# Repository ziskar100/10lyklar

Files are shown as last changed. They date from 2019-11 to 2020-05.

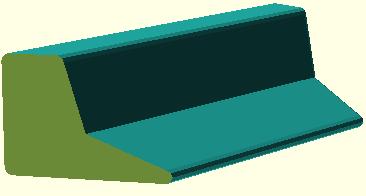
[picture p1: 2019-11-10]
initial_ideas/first_3d_printed_materials/garbage_collector/ArmLeft.jpg

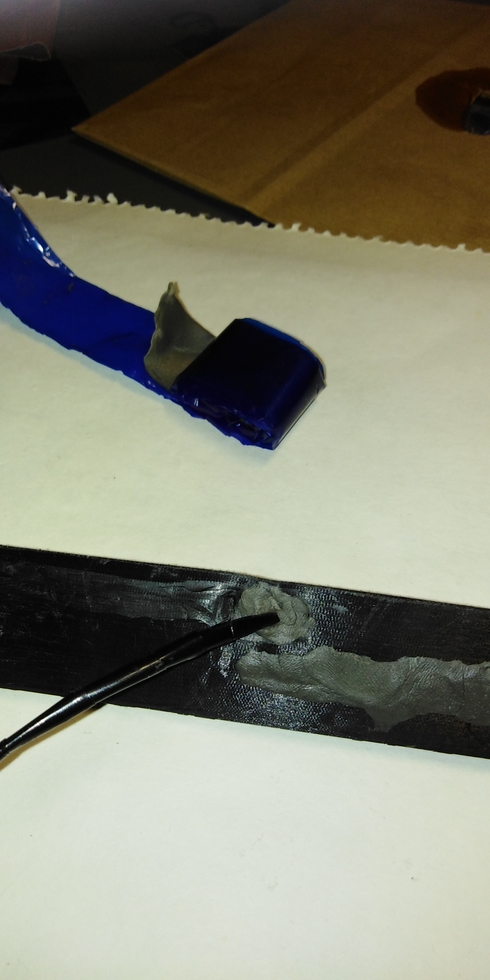
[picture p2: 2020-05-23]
3dprinting/construction_details/dcmotor_cables_at_the exit_of_hull.jpg

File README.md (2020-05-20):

# To Oceanis
Αποθετήριο του 10ου Γενικού Λυκείου Λάρισας για στην συμμετοχή στον Διαγωνισμό Ρομποτικής Ανοιχτών Τεχνολογιών

### Τίτλος έργου
Το SOS των ωκεανών· Η αποστολή του OCEANIS

### Αναλυτική περιγραφή ιδέας:

Η πρότασή μας σχετίζεται άμεσα με το ζήτημα της κλιματικής αλλαγής και ειδικότερα με την Προστασία του περιβάλλοντος. Σήμερα στους ωκεανούς, στα ποτάμια και στις λίμνες συσσωρεύονται  αμέτρητοι τόνοι σκουπιδιών από τις καθημερινές δραστηριότητες του ανθρώπου-καταναλωτή με δραματικά αποτελέσματα για την βιοποικιλότητα των υδάτινων περιβαλλόντων και στην τελική για την ίδια την επιβίωση του ανθρώπινου γένους μακροπρόθεσμα.

Επομένως, καθίσταται επιτακτική η ανάγκη εξεύρεσης λύσης καθαρισμού σημαντικού τουλάχιστον μέρους, των σκουπιδιών για την ανακούφιση των τεράστιων αυτών υδατικών λεκανών.

Για το σκοπό αυτό προτείνουμε ένα πρωτότυπο αυτοκινούμενο θαλάσσιο σκάφος που το ονομάσαμε Oceanis. Αυτό, στην τελική του εκδοχή θα κινείται μέσω ηλιακής ενέργειας αυτόνομα, ενώ στην παρούσα υλοποίηση θα χρησιμοποιηθεί η ανοιχτού τύπου τεχνολογία Arduino. Το σκάφος θα σχεδιασθεί από την αρχή μέσω ανοιχτού λογισμικού CAD (OpenSCAD) και θα εκτυπωθεί εξολοκλήρου στον διαθέσιμο 3D εκτυπωτή ULTIMAKER 3 του σχολείου (δείτε τις ήδη έτοιμες εικόνες του Oceanis στα αρχεία εικόνων του github).

Το Oceanis θα κινείται στο νερό με τη βοήθεια δύο (2) κινητήρων (δείτε τον κατάλογο υλικών) με δυνατότητα ελέγχου τους μέσω εφαρμογής με κινητό. Για την εφαρμογή θα χρησιμοποιηθεί το ανοιχτό λογισμικό AppInventor και η επικοινωνία θα γίνεται με bluetooth (δείτε τον κατάλογο υλικών). Το Oceanis θα συλλέγει τα σκουπίδια μέσω μιας ταινίας - ενός ιμάντα - μεταφοράς που θα κινείται με ειδικό κινητήρα (δείτε τον κατάλογο υλικών) ελεγχόμενο απευθείας από το Arduino.

Παράλληλα το Oceanis θα συλλέγει με δύο (2) ειδικούς αισθητήρες (δείτε τον κατάλογο υλικών) επιστημονικά δεδομένα του υδάτινου περιβάλλοντος (θερμοκρασία και καθαρότητα νερού) και θα τα στέλνει με τη βοήθεια ειδικού αισθητήρα (δείτε τον κατάλογο υλικών) και του Arduino στο cloud σε μια πλατφόρμα IoT που με τη σειρά της θα μας τα διαθέτει μέσω Internet στις συσκευές μας (Η/Υ, tablet, κινητό), ώστε να παρακολουθούμε αυτά τα δεδομένα μέσω γραφικών παραστάσεων.

### Λίστα προτεινόμενου εξοπλισμού:
Ως υλικά hardware θα χρησιμοποιηθούν:

1. Για τον σχεδιασμό και κατασκευή του project Oceanis:
-1x Arduino UNO     [~7€]

-1x Breadboard

-xJumper wires and Resistors

-1x 9 volt battery rechargeable    [~8€]

-1x 9 volt battery connector     [~0.5€]

-1x Bluetooth module HC-06      [~7€]

-1x L293D IC     [~1€]

-2x DC motors     [~6€]

-1x Stepper motor     [~3€]

-1x DS18B20 Waterproof Temperature Sensor    [~3.5€]

-1x Analog Turbidity Sensor for Arduino     [~13€]

-1x ESP8266 wifi module     [~5€]

-1x Fillament for 3d printer     [~17€]

-Μεταφορικά      [~4€]

2. Για τον προγραμματισμό  θα χρησιμοποιηθούν:

-Περιβάλλον προγραμματισμού Arduino IDE (ελεύθερο λογισμικό)

-Περιβάλλον προγραμματισμού AppInventor (ελεύθερο λογισμικό)

-Ρυθμίσεις πλατφόρμας IoT (ελεύθερης πρόσβασης)

### Ενδεικτικό κόστος:
95 Ευρώ

Σε κάθε φάκελο υπάρχει ένα αντίστοιχο Readme όπου εξηγούνται τα περιεχόμενα το φακέλου αυτού.

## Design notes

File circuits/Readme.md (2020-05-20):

## Τι περιέχει ο φάκελος
Στον φάκελο αυτό μπορείτε να πάρετε μια συνολική εικόνα όλου του ηλεκτρονικού σχεδιασμού του έργου. Επίσης υπάρχουν 4 υποφάκελοι που ανά δύο μας δείχνουν λεπτομερειακά τα δύο υποσυστήματα, των κινητήρων και των αισθητήρων νερού, δηλ. μπορείτε να δείτε τις συνδεσμολογίες τους και πως είναι στην πραγματικότητα, αλλά και πως είναι ιδεατά σχηματικά για πλήρη κατανόηση των πραγμάτων.

Ωστόσο, αξίζει τον κόπο να αναφερθούμε εδώ ιδιαίτερα στους δύο αισθητήρες παρακολούθησης του νερού που επιλέχθηκαν για το σκοπό αυτό.
### Αισθητήρας θολότητας ή θολούρας ή θολερότητας (Turbidity Sensor V1.0)
Ο αισθητήρας αυτός προσδιορίζει όσον αφορά την ποιότητα του νερού σε τι επίπεδο βρίσκεται από πλευράς θολότητας. Μπορεί και ανιχνεύει διάφορα αιωρούμενα στερεά σωματίδια (TSS) στο νερό. Αυτό το πετυχαίνει μετρώντας τη διαπερατότητα του φωτός και το ρυθμό σκέδασης που αλλάζει με την ποσότητα των ολικών αιωρούμενων σωματιδίων στο νερό. Όταν αυξάνεται η τιμή του TTS, τότε αυξάνεται το επίπεδο θολότητας του νερού και γενικότερα ενός υγρού.
 
Ο συγκεκριμένος αισθητήρας διαθέτει λειτουργίες εξόδου αναλογικού (Analog) και ψηφιακού (Digital) σήματος. Μπορούμε να επιλέξουμε όποια λειτουργία θέλουμε, καθώς επίσης και να ρυθμίσουμε το κατώφλι (threshold) μέσω ποτενσιόμετρου όταν βρισκόμαστε σε λειτουργία ψηφιακού σήματος.
 
Οι αισθητήρες θολότητας μπορούν να χρησιμοποιηθούν για τη μέτρηση της ποιότητας των υδάτων σε ποτάμια και ρέματα, μετρήσεις λυμάτων και αποβλήτων, έρευνα μεταφοράς ιζημάτων και εργαστηριακές μετρήσεις.

Πηγή: https://wiki.dfrobot.com/Turbidity_sensor_SKU__SEN0189
 
### Αισθητήρας θερμοκρασίας με αδιάβροχο καλώδιο προέκτασης (Waterproof DS18b20 temperature probe temperature sensor 18B20 for Arduino)
 
Κάθε αισθητήρας θερμοκρασίας DS18B20 έχει έναν μοναδικό σειριακό κωδικό 64-bit. Αυτό μας επιτρέπει να συνδέουμε πολλούς αισθητήρες στο ίδιο καλώδιο δεδομένων. Έτσι, μπορούμε να παίρνουμε θερμοκρασία από πολλούς αισθητήρες χρησιμοποιώντας μόνο έναν ψηφιακό pin στο Arduino μας.

Πηγή: https://randomnerdtutorials.com/guide-for-ds18b20-temperature-sensor-with-arduino/

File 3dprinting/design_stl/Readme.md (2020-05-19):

## Τι περιέχει ο φάκελος
Εδώ θα μπορέσετε να κατεβάσετε όλα τα αρχεία πού δημιουργήθηκαν με το FreeCAD σε μορφή stl και κατόπιν να τα εισάγετε στο ειδικό πρόγραμμα Cura  για να δημιουργήσετε από τα αρχεία αυτά τα αντίστοιχα αρχεία τύπου gcode και τα οποία στη συνέχεια μπορείτε να εκτυπώσετε στο 3D Printer.

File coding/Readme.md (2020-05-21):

## Τι περιέχει ο φάκελος
Εδώ θα μπορέσετε να δείτε όλους τους κώδικες. Αναλυτικά θα δείτε τους εξής κώδικες:

### 1. Arduino_Bluetooth_DC_Motors.aia

Είναι ο κώδικας ελέγχου των κινητήρων σε μορφή επεξεργάσιμη μέσα από το περιβάλλον του AppInventor. Μπορείτε να τον κατεβάσετε και να τον εισάγετε ώστε να κάνετε τη δική σας επεξεργασία.

### 2. Arduino_Bluetooth_DC_Motors.apk

Είναι ο κώδικας ελέγχου των κινητήρων σε μορφή εκτελέσιμη. Μπορείτε να τον κατεβάσετε και να τον εγκαταστήσετε στην κινητή συσκευή σας και να την εκτελείτε όποτε θέλετε.

### 3. Motor_Stepper
Είναι ο κώδικας ελέγχου του βηματικού κινητήρα. Μπορείτε να τον χρησιμοποιήσετε για να δοκιμάσετε τη σωστή λειτουργία του. Απαιτείται η ενσωμάτωση της βιβλιοθήκης AFMotor.h

### 4. Motors_DCX2_Stepper_via_Bluetooth
Είναι ο κώδικας ελέγχου μέσω Bluetooth και των τριών κινητήρων. Απαιτείται οπωσδήποτε η ασπίδα ελέγχου των κινητήρων όπως φαίνεται και στις αντίστοιχες εικόνες. Η ασπίδα δίνει δύο ports, το port #1 (M1 & M2) όπου βάζουμε τον βηματικό κινητήρα με τη σειρά των 5 καλωδίων όπως φαίνεται και στην αντίστοιχη εικόνα και το port #2 (M3 & M4) όπου βάζουμε τα 4 καλώδια των DC κινητήρων όπως φαίνεται και στην αντίστοιχη εικόνα (η μεσαία θέση μένει κενή).

Στον κώδικα υπάρχουν αρκετά επεξηγηματικά σχόλια και θεωρείται σχετικά εύκολος στην κατανόηση. Εκείνο που αξίζει να δει κανείς είναι πως γίνεται η ζεύξη μεταξύ του κώδικα του Arduino με τα blocks του AppInventor. Γι αυτό και πρέπει να ανοιχτούν ταυτόχρονα οι δύο κώδικες. 

### 5. Motors_DCX2_via_Bluetooth

Είναι ο κώδικας ελέγχου μέσω Bluetooth των DC κινητήρων. Μπορείτε να τον χρησιμοποιήσετε για να δοκιμάσετε τη σωστή λειτουργία τους. Απαιτείται η ενσωμάτωση της βιβλιοθήκης AFMotor.h

### 7. WEMOS_D1_Wifi_Sensor

Είναι ο κώδικας αποστολής μέσω WiFi των δεδομένων των δύο αισθητήρων του νερού. Παρουσιάζει ιδιαίτερο εκπαιδευτικό ενδιαφέρον και είναι εμπλουτισμένος με αρκετές βιβλιοθήκες! Στο 1ο κομμάτι του ενσωματώνονται οι βιβλιοθήκες που φαίνονται στον κώδικα και επιλέγεται σαν συσκευή (προσοχή εδώ!) όχι το Arduino, αλλά το WEMOS D1 R1.

Στο 2ο κομμάτι εγκαθιδρύονται τα Wifi settings. Χρειάζεται να ξέρουμε για το δίκτυο Internet που συνδεόμαστε δύο πράγματα: To ssid και το password του δικτύου. Τα βάζουμε αντίστοιχα στη θέση των αστεριών.

Στο 3ο κομμάτι εγκαθιδρύονται τα ThingSpeak Settings . Πρέπει να ξέρει ο κώδικας 2 πληροφορίες από την πλατφόρμα ThingSpeak: Το channelID και το writeAPIKey. Εδώ αντικαθιστούμε με τα δικά μας αφού έχουμε ανοίξει λογαριασμό στην πλατφόρμα και φτιάξουμε ένα κανάλι με όσα πεδία επιθυμούμε. Κατόπιν ακολουθεί το setup και μετά το loop.

Στο loop, στο 1ο κομμάτι συλλέγουμε τις τιμές των αισθητήρων και κάνουμε τις κατάλληλες μετατροπές, ειδικά για τη θολότητα. Στο επόμενο κομμάτι δημιουργούμε ένα string που θα έχει όλες τις πληροφορίες ανά πεδίο και τις οποίες θα στείλουμε πάνω στην πλατφόρμα. Τέλος, στέλνουμε τα data στην πλατφόρμα και δημιουργούμε στο τέλος και μια χρονοκαθυστέρηση μεταξύ των αποστολών.

### 8. Water_DS18B20_Temperature_Sensor

Είναι ο κώδικας ελέγχου του αισθητήρα θερμοκρασίας. Μπορείτε να τον χρησιμοποιήσετε για να δοκιμάσετε τη σωστή λειτουργία του. Απαιτείται η ενσωμάτωση των βιβλιοθηκών OneWire.h και DallasTemperature.h

### 9. Water_Turbidity_Analog_Sensor

Είναι ο κώδικας ελέγχου του αισθητήρα θολότητας. Μπορείτε να τον χρησιμοποιήσετε για να δοκιμάσετε τη σωστή λειτουργία του.

### 10. prop-designer
Ο συγκεκριμένος κώδικας μας δίνει τη δυνατότητα να δημιουργούμε παραμετρικά ότι προπέλα επιθυμούμε, όσον αφορά είτε τον αριθμό των λεπίδων της, είτε το πάχος του άξονά της, είτε το μέγεθος του ομφαλού του άξονα κ.α.

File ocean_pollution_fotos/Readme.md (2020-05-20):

## Τι περιέχει ο φάκελος

Εδώ έχουμε μια συλλογή φωτογραφιών με την τεράστια ζημιά που υφίσταται το υδάτινο περιβάλλον και που προέκυψαν από την έρευνά μας.

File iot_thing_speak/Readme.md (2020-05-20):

## Τι περιέχει ο φάκελος
Εδώ θα μπορέσετε να δείτε δύο χαρακτηριστικές εικόνες από την πλατφόρμα ThingSpeak.

Η 1η δείχνει ένα στιγμιότυπο από τις 3 γραφικές παραστάσεις των μεγεθών που μετρούνται από τους αισθητήρες του νερού.

Η 2η  δείχνει μια από τις εξελιγμένες δυνατότητες που έχει η συγκεκριμένη πλατφόρμα.

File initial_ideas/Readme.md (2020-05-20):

## Τι περιέχει ο φάκελος
Εδώ θα μπορέσετε να δείτε:

1.  Μια εικόνα όλων παραγγελθέντων ειδών

2. Μια εικόνα όλων των εργαλείων που χρησιμοποιήθηκαν για την κατασκευή του έργου. Λείπει από την εικόνα το κολλητήρι.

3. Δύο υπο-φακέλους που αφορούν την αρχική φάση του έργου. Ο ένας περιέχει όλες τις αρχικές σκέψεις αποτυπωμένες στο χαρτί. Ο άλλος περιέχει αρχικές 3D εκτυπώσεις κομματιών του σκάφους, ώστε να πάρουμε μια αρχική ιδέα τι πρέπει να φτιάξουμε στη συνέχεια.

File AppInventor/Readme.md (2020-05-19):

## Τι περιέχει ο φάκελος
Εδώ θα μπορέσετε να δείτε δύο χαρακτηριστικές εικόνες από την εφαρμογή το AppInventor, η μία αφορά στο σχεδιασμό και η άλλη αφορά τα blocks (κώδικα).

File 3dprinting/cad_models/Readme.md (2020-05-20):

## Τι περιέχει ο φάκελος
Εδώ θα μπορέσετε να δείτε όλα τα επιμέρους σχέδια που εκπονήθηκαν με το ελεύθερο λογισμικό FreeCAD καθώς επίσης και με το OpenSCAD. Όσον αφορά το FreeCAD  μπορείτε να   πάρετε περισσότερες πληροφορίες από τον σύνδεσμο:
 
https://www.secnews.gr/202551/freecad-0-18-4-open-source-3d-dorean-cad-gia-olous/
 
Το FreeCAD είναι μια εφαρμογή CAD ανοικτού κώδικα που έχει σαν κύριο στόχο την μηχανολογική ανάπτυξη και το βιομηχανικό σχέδιο.
Σε αυτό βοηθάει ο αρθρωτός σχεδιασμός που επιτρέπει πάρα πολλές παραμετροποιήσεις για να χρησιμοποιηθεί και σε άλλες εφαρμογές. Υποστηρίζεται από μία πολύ δυναμική κοινότητα,  είναι γραμμένο σε Python και διατίθενται πάρα πολλά tutorials.

Όσον αφορά το Openscad όπως μας πληροφορεί και η ιστοσελίδα του ellak
 
https://openhardware.ellak.gr/2017/01/18/openscad-mia-efarmogi-eleftherou-logismikou-gia-3d-modeling/
 
είναι ένα λογισμικό για τη δημιουργία τρισδιάστατων CAD μοντέλων. Είναι ελεύθερο λογισμικό και διατίθεται σε διάφορες εκδόσεις για διαφορετικές πλατφόρμες λογισμικών, Linux/UNIX, Windows και Mac OS X και  εξαιρετικά χρήσιμο για όσους τυπώνουν 3D αντικείμενα και χρειάζονται ένα λογισμικό επεξεργασίας (για αρχεία του αποθετηρίου Thingiverse) και 3D modeling.

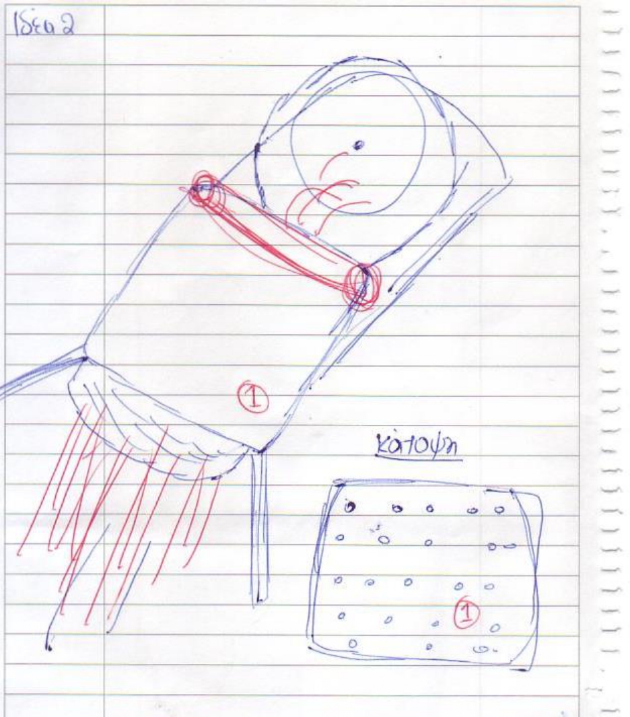
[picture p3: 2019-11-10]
initial_ideas/paper_sketch_plans/plan2.jpg

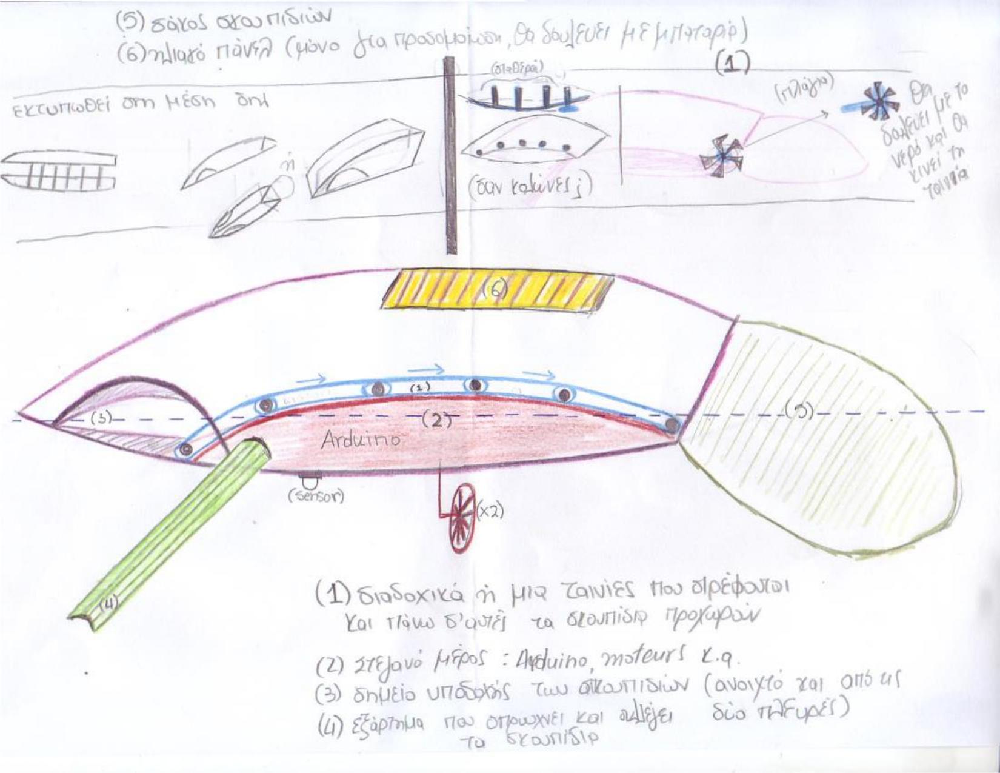
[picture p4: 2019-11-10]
initial_ideas/paper_sketch_plans/plan6.jpg

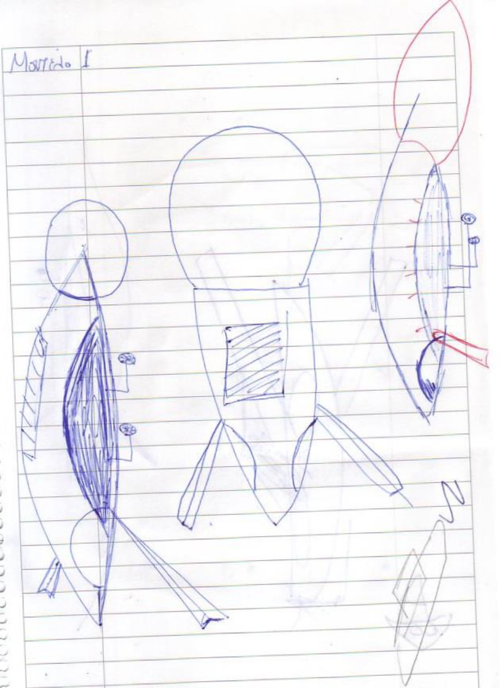
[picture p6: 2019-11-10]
initial_ideas/paper_sketch_plans/plan4.jpg

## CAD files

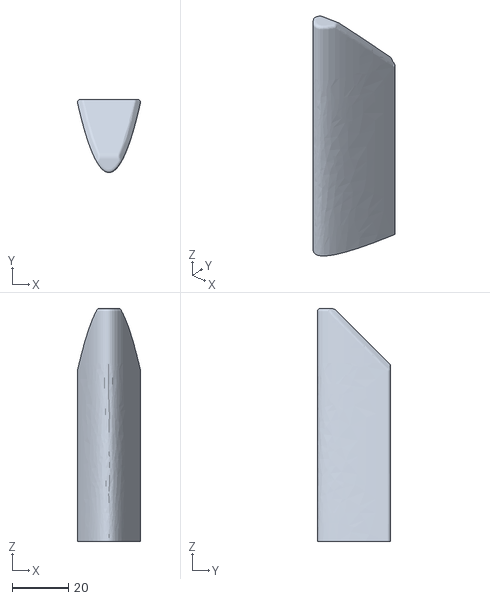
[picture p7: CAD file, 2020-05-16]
3dprinting/design_stl/Hull_Front.stl
22.5 x 26.0 x 83.0

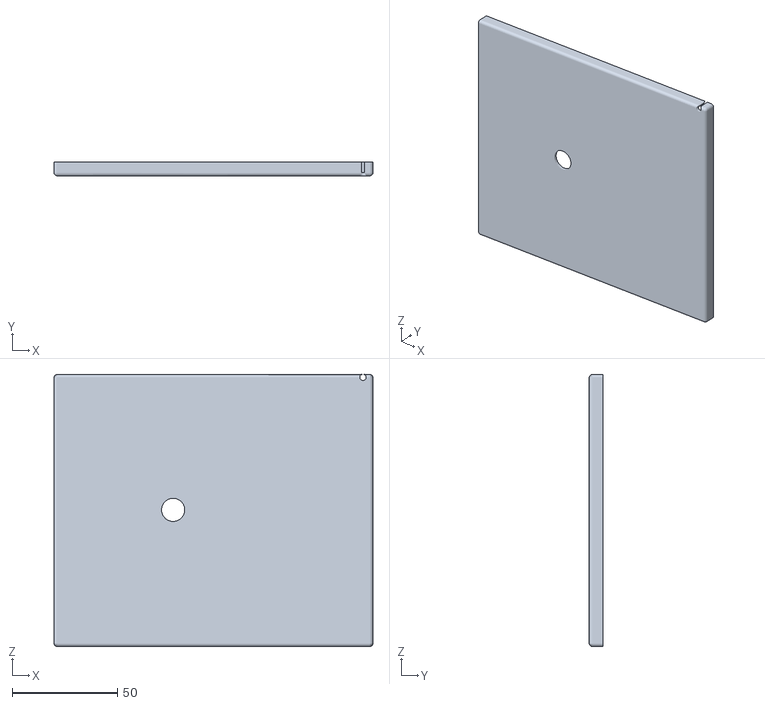
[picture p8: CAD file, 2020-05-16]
3dprinting/design_stl/ControlBoxCover.stl
151.3 x 6.50 x 129.0

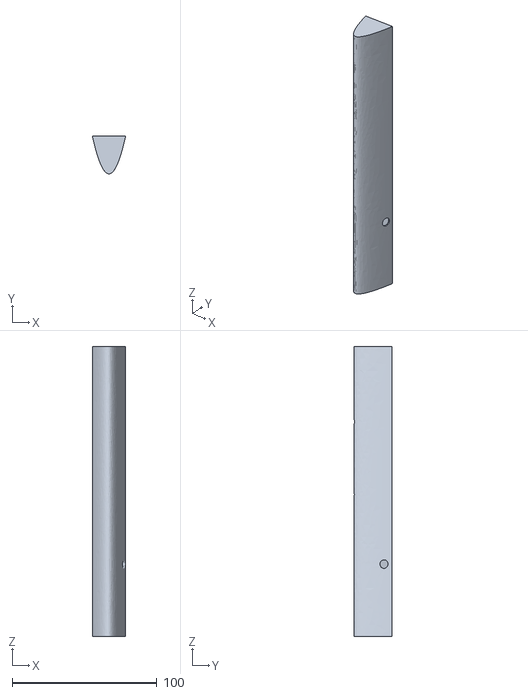
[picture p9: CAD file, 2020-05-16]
3dprinting/design_stl/Hull_Back_Left.stl
23.0 x 26.0 x 200.5

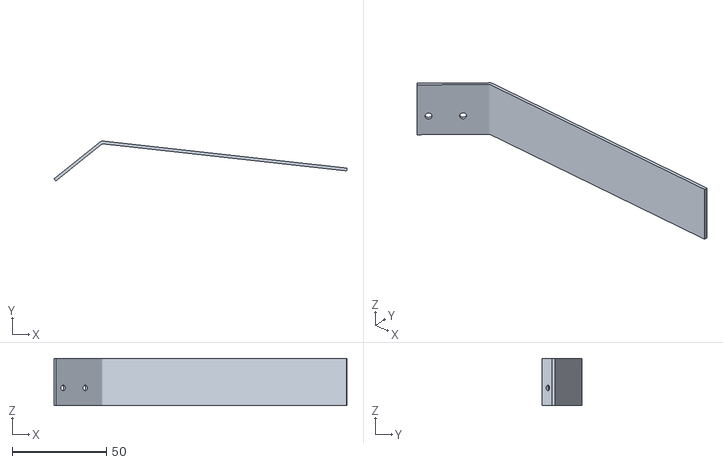
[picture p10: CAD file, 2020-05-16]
3dprinting/design_stl/ArmLeft.stl
155.3 x 21.2 x 25.0

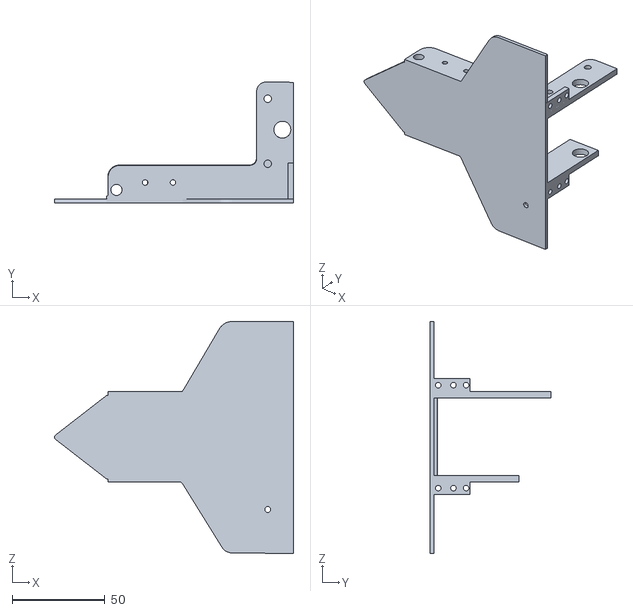
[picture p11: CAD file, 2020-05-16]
3dprinting/design_stl/ForeSection.stl
128.8 x 65.1 x 125.0

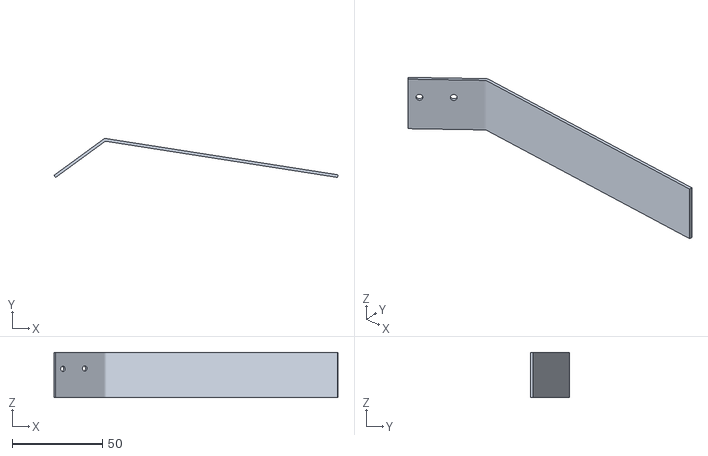
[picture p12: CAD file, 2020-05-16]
3dprinting/design_stl/ArmRight.stl
157.0 x 21.6 x 25.0

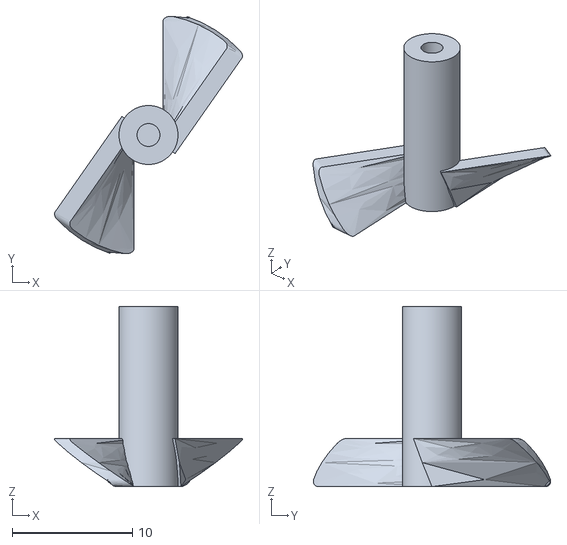
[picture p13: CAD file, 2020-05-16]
3dprinting/design_stl/Propeller.stl
15.6 x 19.7 x 15.0

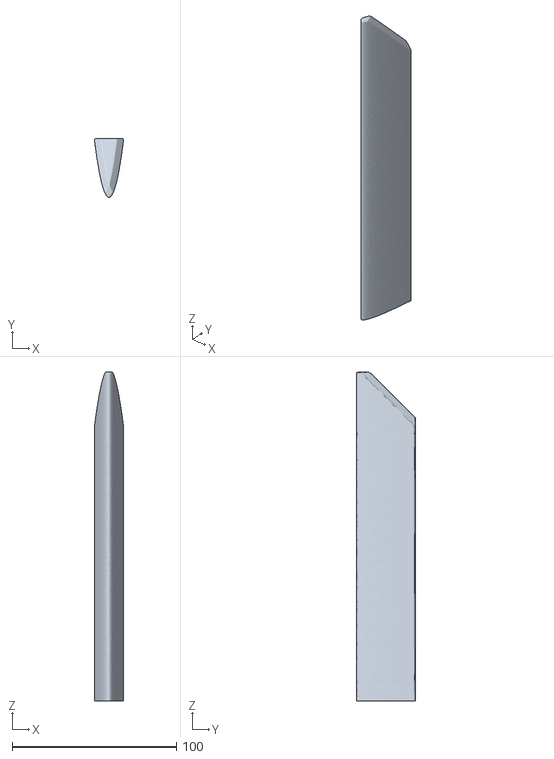
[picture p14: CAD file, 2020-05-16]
3dprinting/design_stl/Hull_Middle.stl
17.7 x 36.0 x 200.5

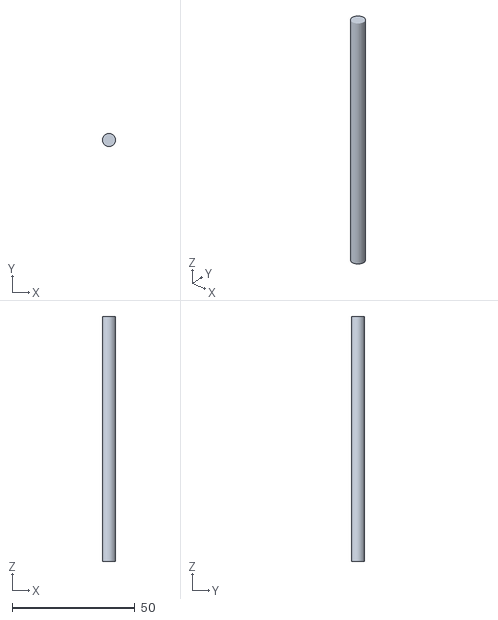
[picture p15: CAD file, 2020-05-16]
3dprinting/design_stl/AxisNormal.stl
5.38 x 5.39 x 100.0

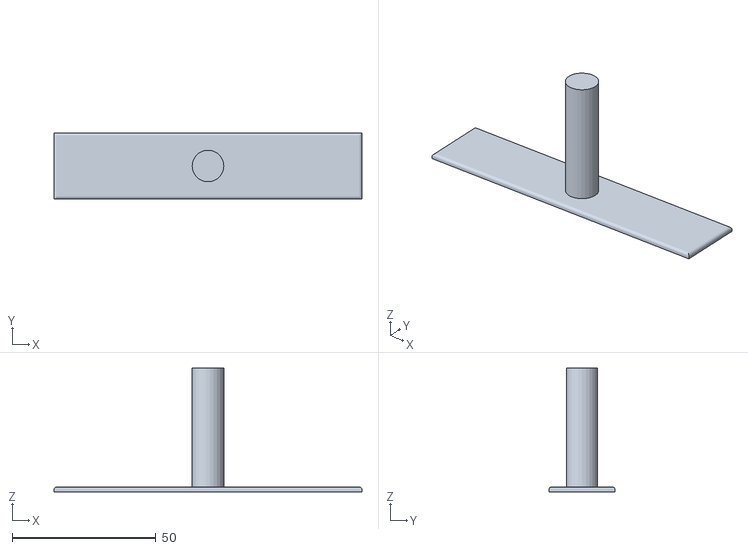
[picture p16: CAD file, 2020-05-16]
3dprinting/design_stl/SupportHelper.stl
107.0 x 23.0 x 43.0

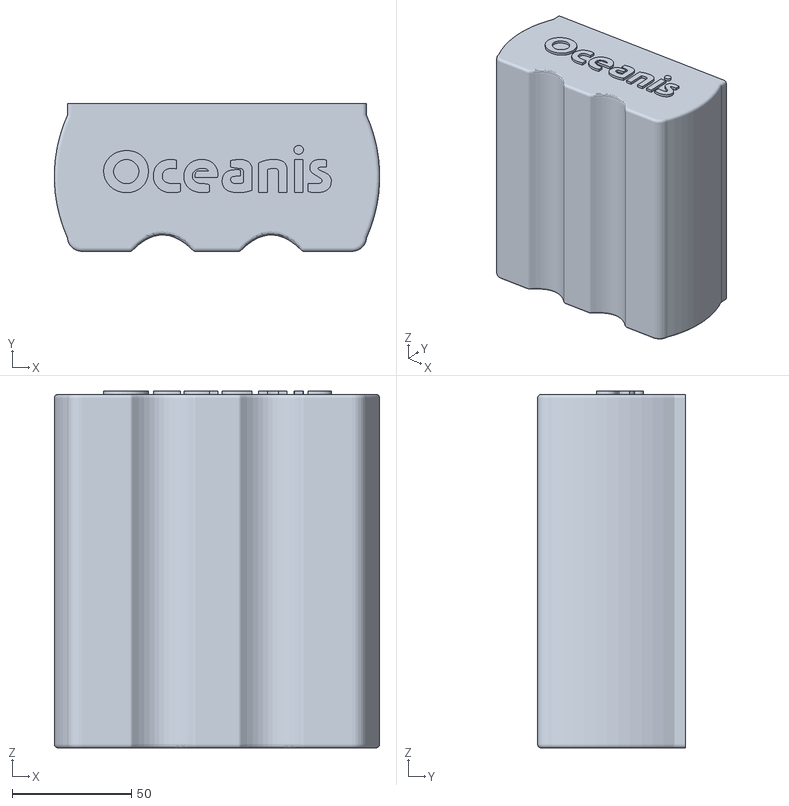
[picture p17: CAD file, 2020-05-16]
3dprinting/design_stl/ControlBox.stl
136.3 x 61.9 x 149.6

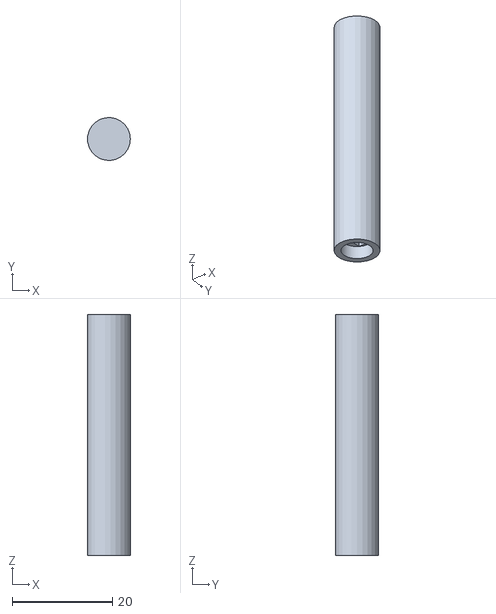
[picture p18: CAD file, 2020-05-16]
3dprinting/design_stl/AxisStepper.stl
8.53 x 8.54 x 48.0

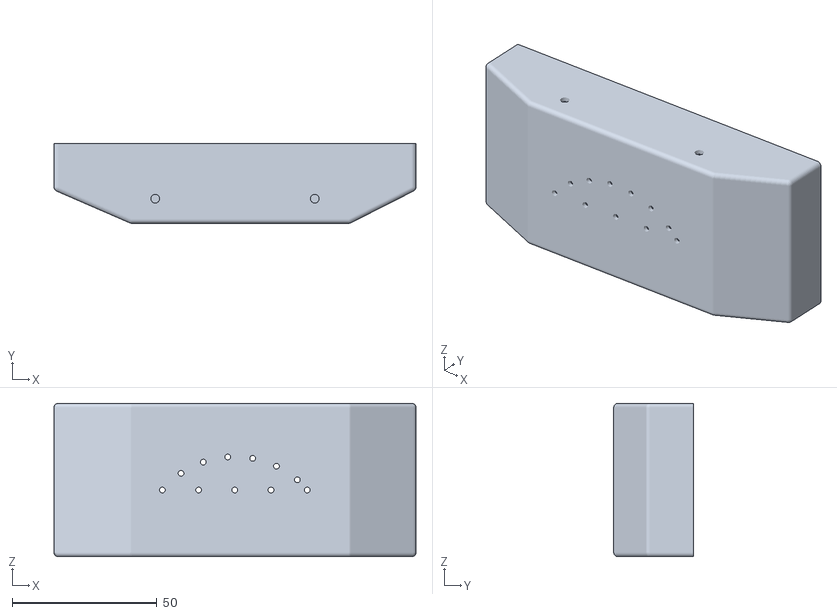
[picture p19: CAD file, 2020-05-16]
3dprinting/design_stl/Dumpster.stl
125.0 x 27.5 x 53.0

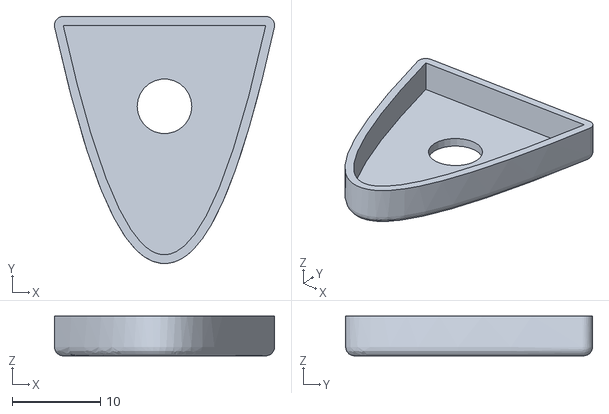
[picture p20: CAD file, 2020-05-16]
3dprinting/design_stl/HullCover.stl
25.0 x 28.0 x 4.50

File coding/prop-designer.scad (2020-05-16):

$fn=360;
echo ("--------------------------------");
noofblades=3;// 3 to 20
echo("Number of blades is: ",noofblades);
stepsize=360/noofblades;
echo("step size is: ",stepsize);
shaftheight=15;
echo("shaft height is: ",shaftheight);
shaftdiameter=4;
echo("shaft diameter is: ",shaftdiameter);
bladelength=15;
echo("blade length is: ",bladelength);
echo ("--------------------------------");

for(angle= [0:stepsize:360]){
   rotate([0,0,angle])
   prop();
}  
//create the propshaft
difference(){
translate([0,0,-4])
cylinder(d=shaftdiameter+4,h=shaftheight);
translate([0,0,-5])
cylinder(d=shaftdiameter,h=shaftheight+2);
}


module prop(){
linear_extrude(
  height = 8, 
  center = true,
  convexity = 80, 
  twist = 50
  ) 
translate([2, 0, 0])

square([1.5,bladelength]);
}

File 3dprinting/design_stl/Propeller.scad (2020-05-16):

$fn=360;
echo ("--------------------------------");
noofblades=2;// 3 to 20
echo("Number of blades is: ",noofblades);
stepsize=360/noofblades;
echo("step size is: ",stepsize);
shaftheight=15;
echo("shaft height is: ",shaftheight);
shaftdiameter=1.9;
echo("shaft diameter is: ",shaftdiameter);
bladelength=10;
echo("blade length is: ",bladelength);
echo ("--------------------------------");

for(angle= [0:stepsize:360])
  {
   rotate([0,0,angle])
   prop();
}  
//create the propshaft
difference()
{
translate([0,0,-2])
cylinder(d=shaftdiameter+3,h=shaftheight);
translate([0,0,0])
cylinder(d=shaftdiameter,h=shaftheight);
}

module prop()
{
linear_extrude(
  height = 4, 
  center = true,
  convexity = 80, 
  twist = 35
  ) 
translate([1.2, 0, 0])

square([1.5,bladelength]);
}

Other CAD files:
3dprinting/design_stl/Hull_Back_Right.stl
3dprinting/design_stl/FlagO.stl

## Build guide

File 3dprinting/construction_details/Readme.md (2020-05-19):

## Τι περιέχει ο φάκελος
Εδώ θα μπορέσετε να δείτε ακόμη περισσότερες λεπτομέρειες πάνω στα σχέδια που εκπονήθηκαν με το FreeCAD. Eπιλέχθηκαν ορισμένες πολύ ενδιαφέρουσες λεπτομέρειες που έδωσαν στο τελικό έργο  είτε μία αισθητική άποψη, είτε επέλυσαν τεχνικά ζητήματα.

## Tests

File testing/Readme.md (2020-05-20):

## Τι περιέχει ο φάκελος

Εδώ θα μπορέσετε να δείτε τα διάφορα tests που υποβάλαμε στα διάφορα τμήμα του έργου για να διαπιστώσουμε την καλή λειτουργία τους. Αυτό είναι απαραίτητο να γίνει ώστε αν κάτι δεν δουλεύει σωστά να ξέρουμε σε ποιο τμήμα του έργου βρίσκεται η βλάβη.

Έτσι τεστάραμε ξεχωριστά τον βηματικό κινητήρα με τον ιμάντα μεταφοράς, τους 2 DC κινητήρες, τους δύο αισθητήρες νερού, την πλατφόρμα ThingSpeak, το βύθισμα του σκάφους με τα έρμα και την πλεύση και ισορροπία του σκάφους.

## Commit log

2020-03-27 Create Motors DCX2 via Bluetooth
2020-03-27 Create Motors DCX2, Stepper via Bluetooth
2020-03-27 Create Motor Stepper
2020-03-27 Create Water DS18B20 Temperature Sensor
2020-03-27 Create Water Turbidity Analog Sensor
2020-03-27 Create WEMOS D1 Wifi Sensor
2020-03-27 Update WEMOS D1 Wifi Sensor
2020-04-19 Update Motors DCX2, Stepper via Bluetooth
2020-05-12 Create G:\Προσωπικά\Βθμια Εκπαίδευση\10o Λύκειο\Παράλληλες δραστηριότητες\2019 ΕΕΛΛΑΚ, 2ος Πανελλήνιος Διαγωνισμός Ρομποτικής\10lyklar_github_repo\ocean_pollution_fotos\test
